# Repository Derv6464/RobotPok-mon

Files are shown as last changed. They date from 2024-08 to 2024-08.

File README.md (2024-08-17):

# Life Size Fuecoco Robot
This is a fully 3d printed robotic Fuecoco Pokemon. It can be controlled over wifi using a custom bulit contoller or a website

This was a college project for Immersive Software Engineering CS4445 and for a cosplay for Dubin Comic Con 2024.

The full project can be found on the college branch, it will include extra things like the website, interfacing with aws and a full report.

This branch has everything needed to 3d print and assemble the robot and control it using the custom controller.

## 3D Printing & laser cutting
This was printed using an Ender3 v2.
The model has been split up to fit in the 220mm * 220mm * 250mm build volume of the Ender3 v2
The orginal fuecoco model was found [here](#)

All the STL files can be found [here](#)

The top of the conrollet was laser cut from 3mm clear acrylic so the LEDs could shine through
This could be 3d printed if a laser cutter is not accessible

note the head has weird slots on the back, ingnore them and glue magnets instead

## Assembly

- 3d print all the parts
- do a lot of sanding and filling
- glue the parts together
- do more sanding and filling
- spray paint
- do more sanding and filling
- do the final coat of spray paint 
- assemble the electronics (see wiring diagram and code setup)
- put the electronics in the pokemon
- glue in the electornics
- glue on the magnets

## Wiring Diagram
tbd
solder pico headers up

## Code Setup
I used MicroPython on the Raspberry Pi Pico W
The code for the pokemon can be found [here](#)
Copy it over from the computer to the Raspberry Pi Pico W
Change the wifi ssid and password in the code
Run the code
The controller and fuecoco need to be on the same wifi network
fuecoco runs an api and the the controller sends requests to the api. When the fuecoco receives a request it moves the motors accordingly

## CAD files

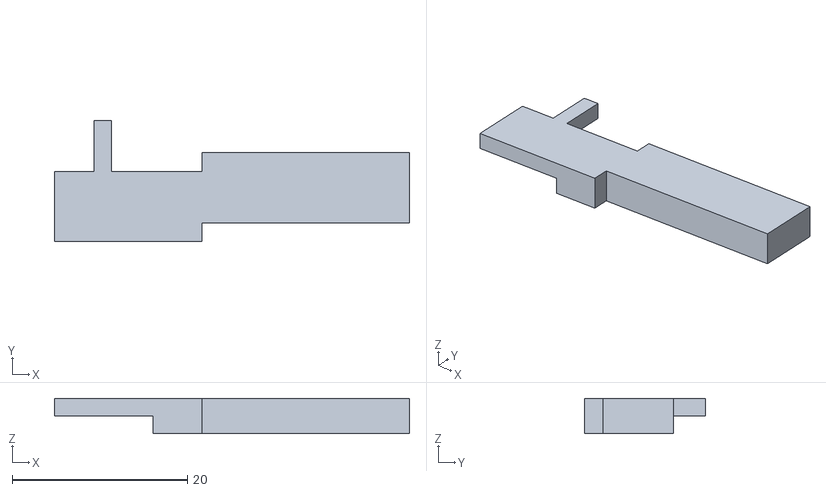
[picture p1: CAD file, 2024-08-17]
Controller/CAD/STL/TopAnalogStickHolder.stl
40.5 x 13.9 x 4.00

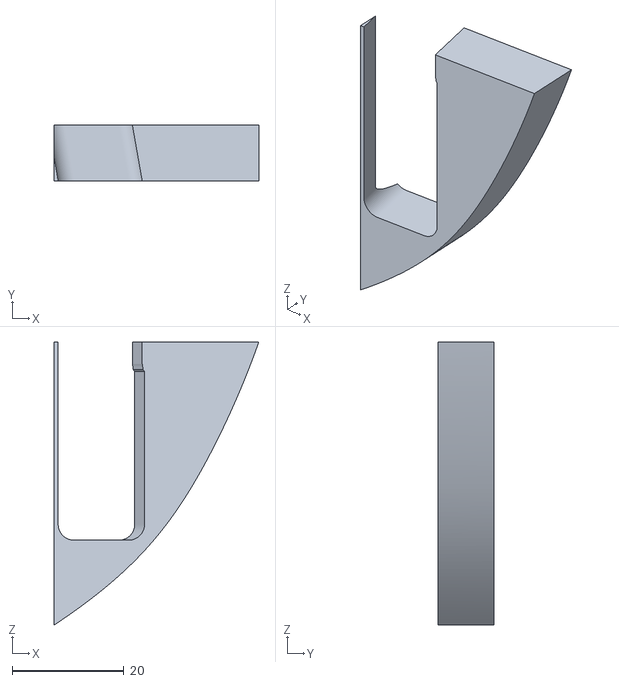
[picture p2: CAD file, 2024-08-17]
Fuecoco/CAD/STL/Tail 6AA battery holder p1.stl
36.6 x 10.0 x 50.6

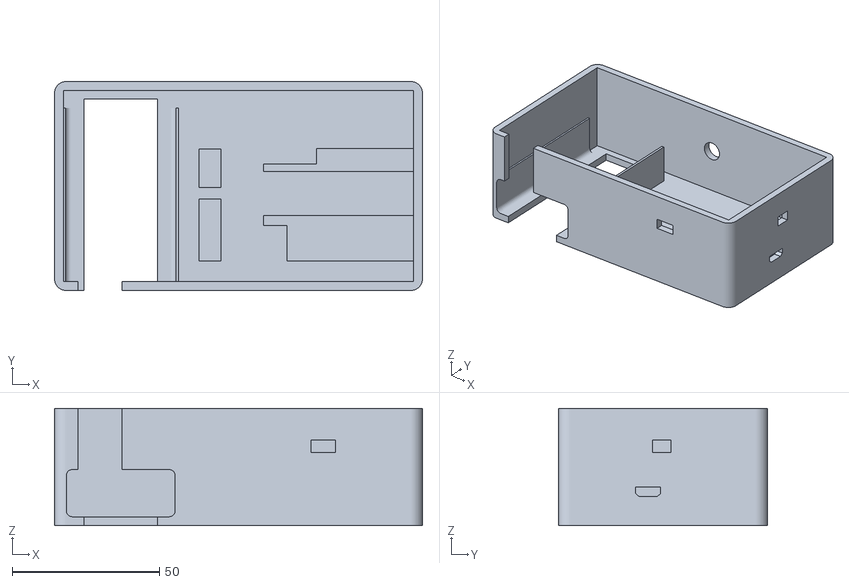
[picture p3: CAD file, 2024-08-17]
Controller/CAD/STL/ContollerBody.stl
125.0 x 71.0 x 39.8

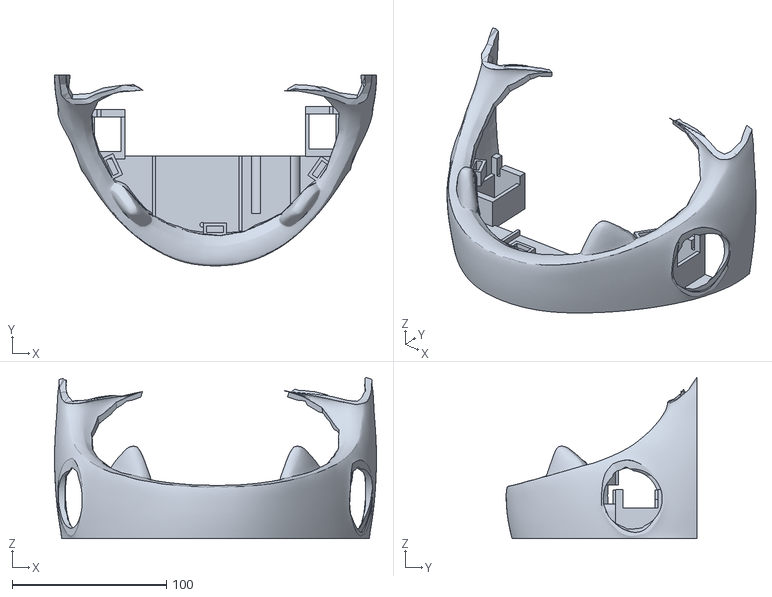
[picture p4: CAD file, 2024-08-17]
Fuecoco/CAD/STL/Chin.stl
209.0 x 123.8 x 104.6

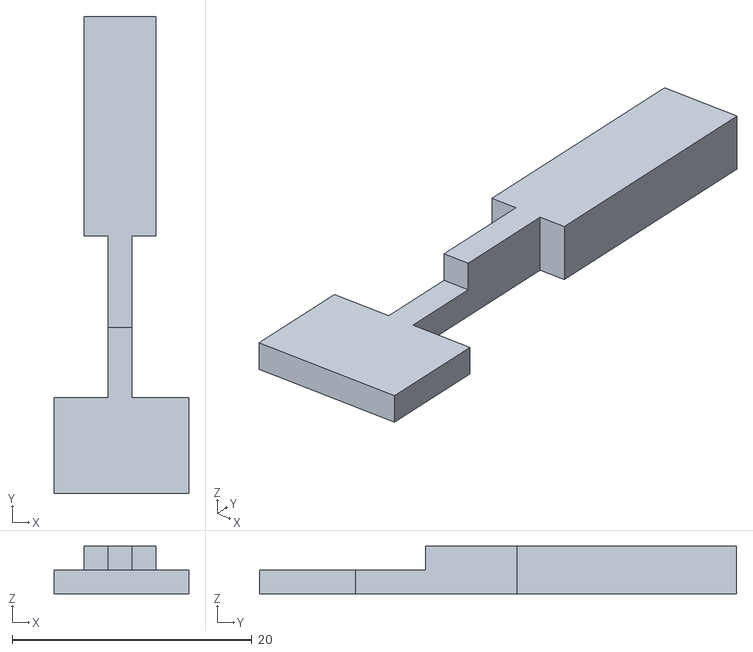
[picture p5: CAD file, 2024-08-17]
Controller/CAD/STL/BottomAnalogStickHolder.stl
11.2 x 39.8 x 4.00

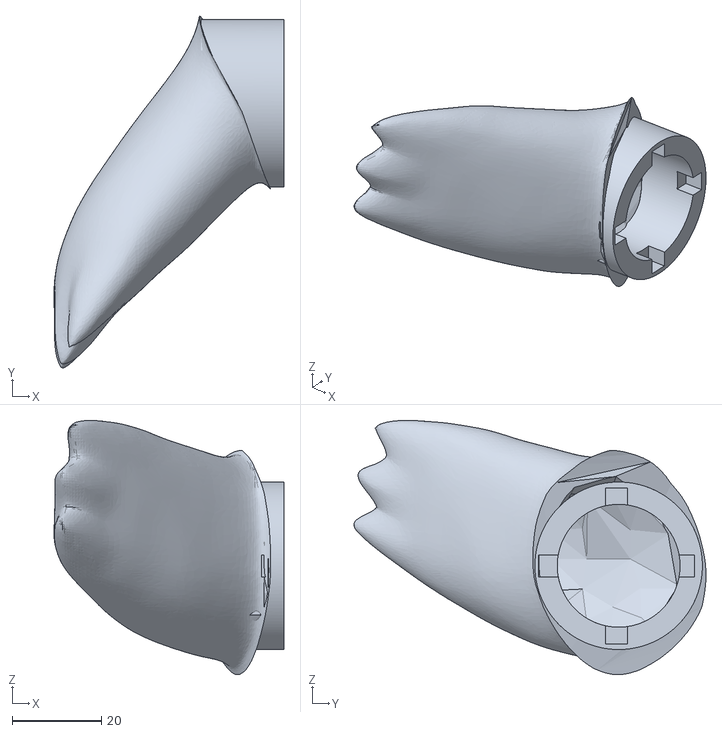
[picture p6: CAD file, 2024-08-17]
Fuecoco/CAD/STL/LeftArm.stl
51.4 x 78.8 x 56.9

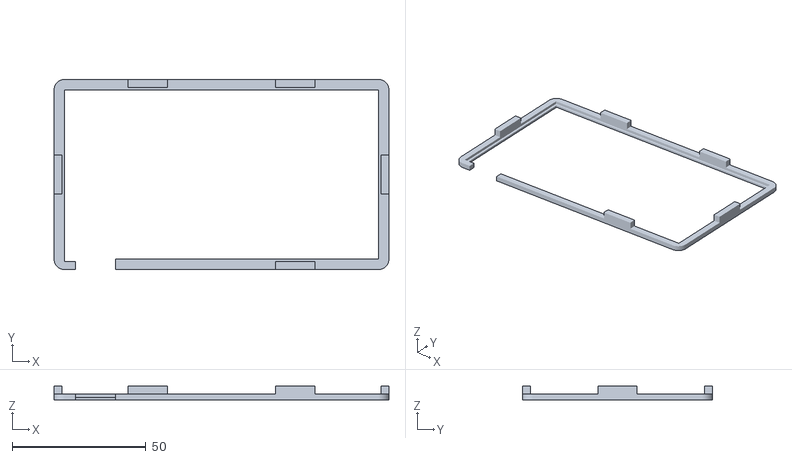
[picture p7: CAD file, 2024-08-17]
Controller/CAD/STL/nOOdHolder.stl
125.0 x 71.0 x 5.20

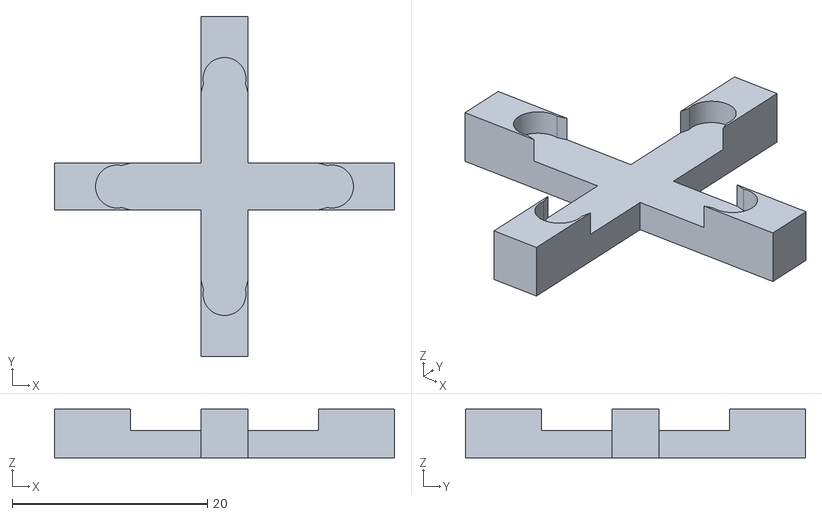
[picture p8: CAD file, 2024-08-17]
Fuecoco/CAD/STL/ArmToServo.stl
34.8 x 34.8 x 5.00

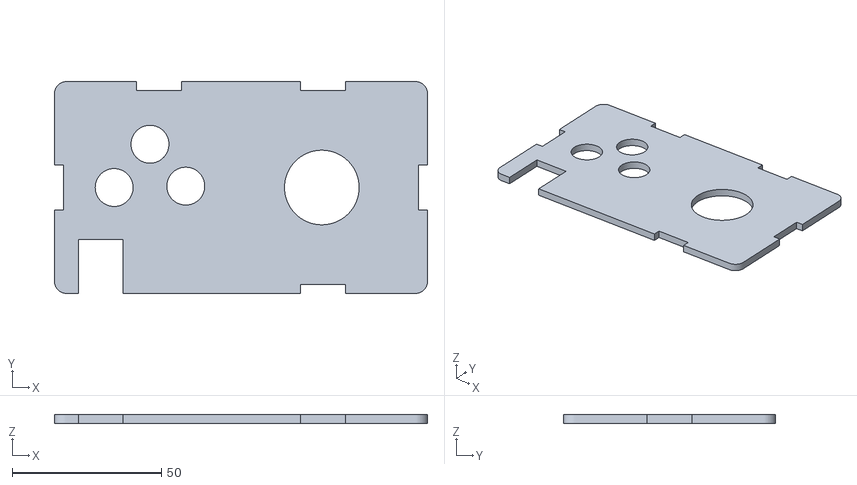
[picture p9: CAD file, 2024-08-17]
Controller/CAD/STL/Cover.stl
125.0 x 71.0 x 3.00

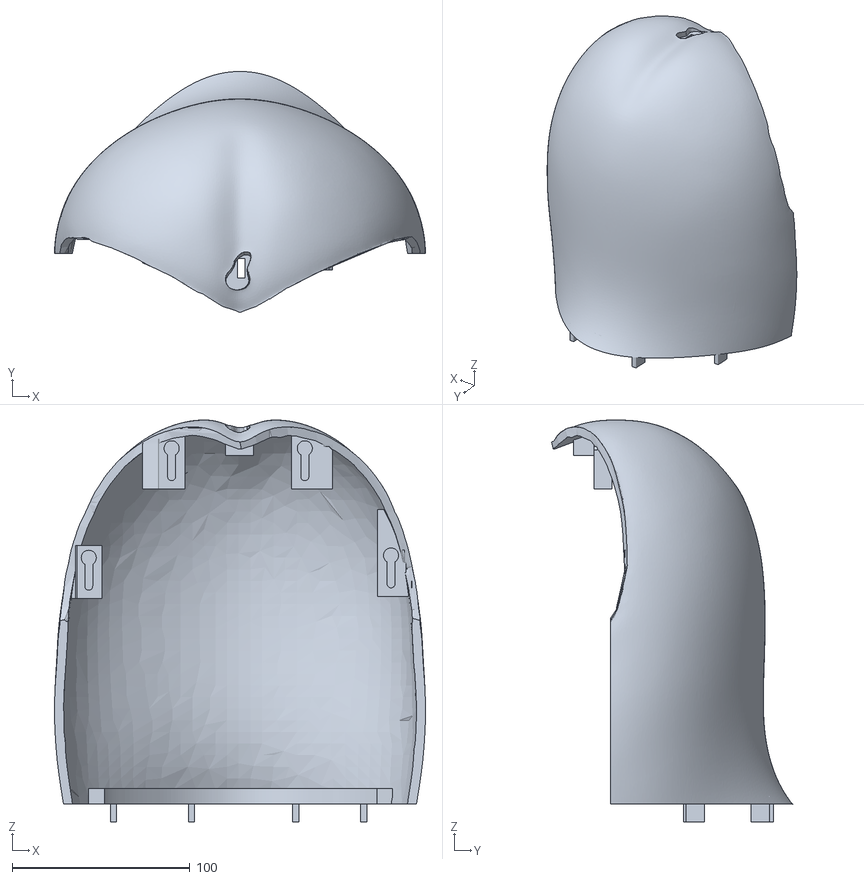
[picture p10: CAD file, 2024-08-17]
Fuecoco/CAD/STL/Body.stl
208.9 x 135.8 x 226.4

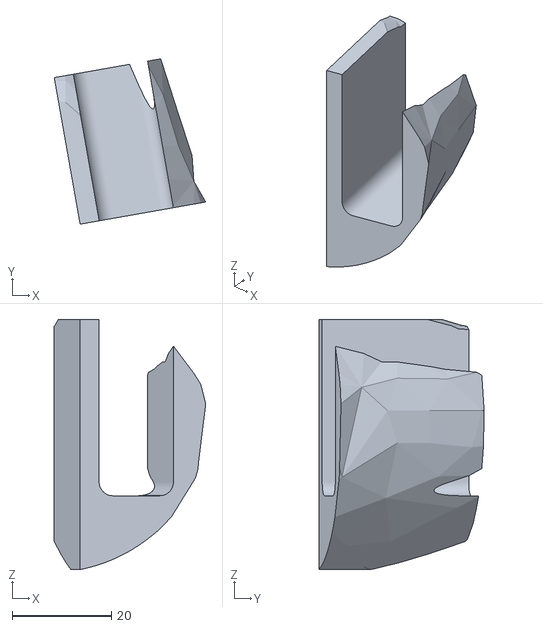
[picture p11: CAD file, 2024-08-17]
Fuecoco/CAD/STL/Tail 6AA battery holder p2.stl
30.5 x 33.3 x 50.4

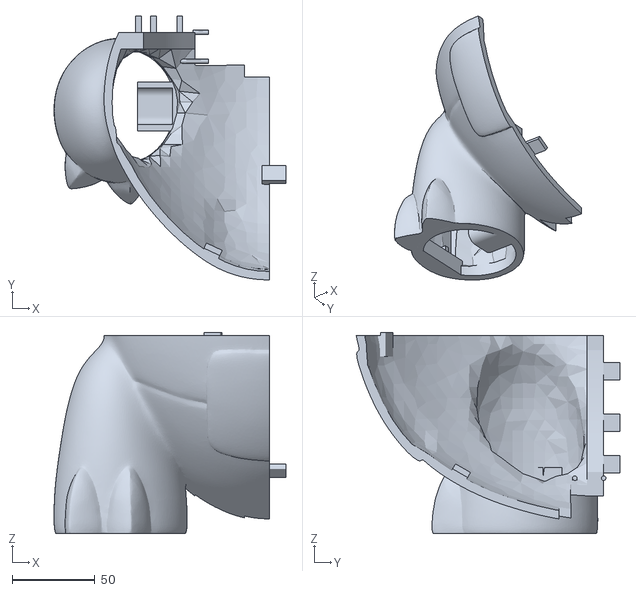
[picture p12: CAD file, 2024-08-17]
Fuecoco/CAD/STL/LeftLeg.stl
140.3 x 159.5 x 121.8

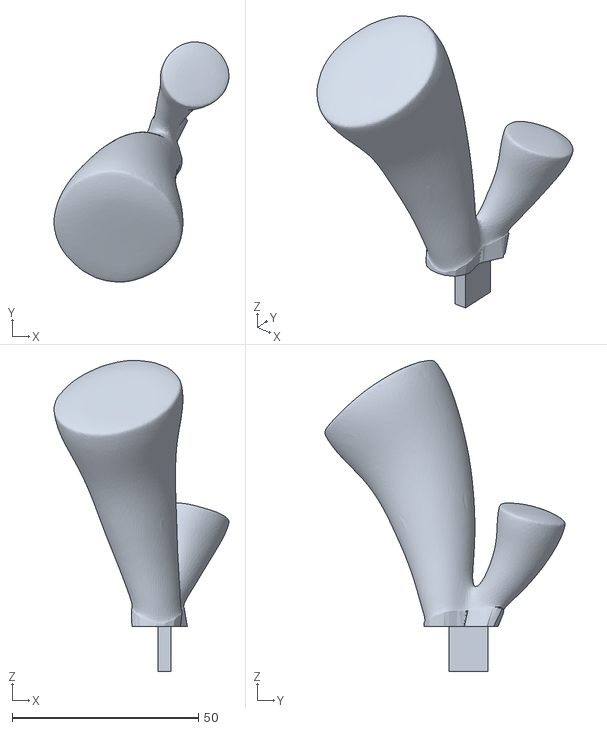
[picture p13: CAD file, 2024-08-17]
Fuecoco/CAD/STL/HeadFlame.stl
47.0 x 64.5 x 83.5

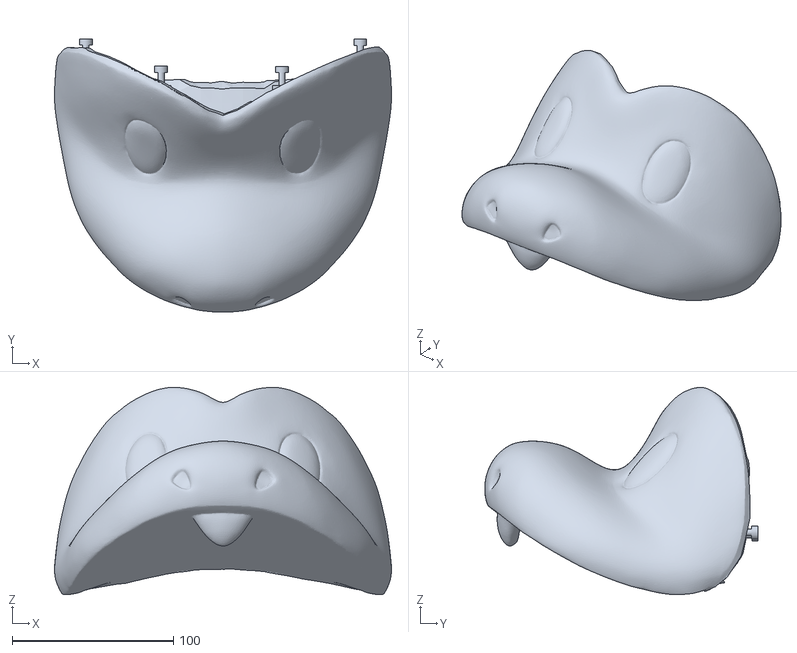
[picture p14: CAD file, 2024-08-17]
Fuecoco/CAD/STL/Head.stl
209.0 x 169.6 x 128.5

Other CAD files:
Fuecoco/CAD/STL/Tail.stl
Fuecoco/CAD/STL/RightLeg.stl
Fuecoco/CAD/STL/Tail 3AAA battery holder.stl
Fuecoco/CAD/STL/RightArm.stl
Controller/CAD/f3d/Controller.f3z

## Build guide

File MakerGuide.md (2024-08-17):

# How to make Fuecoco

## Parts

### Electronics

| Part | Quantity | Used in | link |
|---|---| ---| -----|
|Raspberry Pi Pico W| 2 | Pokemon and Controller | [Link](https://thepihut.com/products/raspberry-pi-pico-w) |
|Kitronik Motor Driver Board| 1 | Pokemon | [Link](https://kitronik.co.uk/products/5329-kitronik-compact-robotics-board-for-raspberry-pi-pico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) |
|Servo Motor| 2 | Pokemon | [Link](https://thepihut.com/products/towerpro-servo-motor-sg90-digital) |
|TT Hobby Motor| 3| Pokemon | [Link](https://thepihut.com/products/dc-gearbox-motor-tt-motor-200rpm-3-to-6vdc) |
| 6AA Battery Holder| 1 | Pokemon | [Link](https://www.digikey.ie/en/products/detail/mpd-memory-protection-devices/BH16AAW/857244) |
| 3AAA Battery Holder| 2 | Pokemon and Controller | [Link](https://thepihut.com/products/3-x-aaa-battery-holder-with-on-off-switch-and-2-pin-jst) |
|Neopixel Strip| 1 | Pokemon | [Link](https://thepihut.com/products/adafruit-neopixel-digital-rgb-led-strip-white-60-led-white) |4
| Buttons | 4 | Controller | [Link](https://www.mouser.ie/ProductDetail/Shin-Chin/R13-510A-05-BB?qs=F3UvtXhGJLNb6k88C5W3XA%3D%3D) |
| Joystick | 1 | Controller | Taken from broken controller |
| LEDs | 1 | Controller | Any |
| Light n00d | 1 | Controller | [Link](https://thepihut.com/products/noods-flexible-led-filament-3v-300mm-warm-white) |
| Solderable breadboard | 1 | Controller | [Link](https://thepihut.com/products/adafruit-perma-proto-half-sized-breadboard-pcb-single) |
| resistors | 1 | Controller | 330 ohm |

### Other Parts

| Part | Quantity | Used in | link |
|---|---| ---| -----|
| Lego Wheel | 3 | Pokemon | 
| Lego Wheel Holder | 3 | Pokemon |
| Lego Wheel Axle | 3 | Pokemon |
| Lego Wheel Axle Holder | 3 | Pokemon |
| LED Holder | 2 | Controller | 
| Magnets | 4 | Pokemon |
| Lots of hot glue | | Pokemon and Controller | Any |
| Lots of filler | | Pokemon | [Link](https://www.halfords.ie/motoring/paints-body-repair/fillers-preparation/holts-cataloy-knifing-putty-100g-154211.html) |
| Red spray paint | 1 | Pokemon | [Link](https://allcitygraffiti.com/products/red-madrid-94?variant=3243807178792) |
| Black spray paint | 1 | Pokemon | [Link](https://allcitygraffiti.com/products/black-94) |
| White spray paint | 1 | Pokemon | [Link](https://allcitygraffiti.com/products/white-94) |
| off white spray paint | 1 | Pokemon | [Link](https://allcitygraffiti.com/products/blanco-hueso-94) |
| yellow spray paint | 1 | Pokemon | [Link](https://allcitygraffiti.com/products/medium-yellow-94?variant=3243953881128) |
| light pink spray paint | 1 | Pokemon | [Link](https://allcitygraffiti.com/products/rosa-boreal-94?variant=3244061720616) |
| dark pink spray paint | 1 | Pokemon | [Link](https://allcitygraffiti.com/products/rosa-stereo-94?variant=3246509293608) |

All lego parts gotten from the lego mindstorms kit

## 3D Printing & laser cutting

It was just alot of sanding and filling, I spent about 40hr sanding and filling

1. 3d print all the parts (note these aren't the best models and have some issues)
print pic
2. do a lot of sanding and filling
sanding and filling pic
3. glue the legs, tail, body and chin together
glue pic
4. do more sanding and filling
sanding and filling pic
5. spray paint with primer
6. do more sanding and filling
7. do a coat of red colour
8. do more sanding and filling for any imperfections
9. do the final coat of spray paint

The order of the final coat colours I did was:

| Paint | Part| Colour |
|---|-----| ---|
|white primer everywhere| All | white |
|coat of red on body to see imperfections | Body | Red |
|bone white on the face | Head| Bone White |
|red on the arms | Arms | Red |
|light pink on the toungue | Tongue | Light Pink |
|white on the teeth, tape off| Head, Body  | White |
|sprayed the eyes with white, tape off | Head | White |
|sprayed the roof of the mouth dark pink, tape off | Head | Dark Pink |
|dark pink on the inner chin, lip area, tape off | Head | Dark Pink |
|sprayed the inner eyes with black, tape off | Head | Black |
|sprayed the nail area's of the feet with black, tape off | Body | Black |
|sprayed the square area's on the front and tail with yellow, tape off | Body | Yellow |
|bone white on the underbelly, tape off | Body | Bone White |
|red on the rest of the body| Body | Red |

But do whatever works

## Assembly

### Magnets

Orginall there was going to be a sloting system for the hesd to go on the body, hence the weird slots on the back of the head. I ended up glueing magnets in the head and body to hold it together.

I used the lower two slots, did a lot of sanding to make the magnets flush with the body and head and then glued them in with super glue, hot glue and then more super glue.

### Arms

1. The arms to servo parts should connect to a servo cross style servo horn. 
2. Glue these parts together.
3. The arm to servo part can then be sloted into the arms of the pokemon.
4. These should also be glued
5. The arms can be placed into the body, the servo's should be able to be slotted into the holders on the inside of the body

### Motor Assembly

This is not the easiest thing to do

#### Tail Motor

1. Create the lego structure for the motors, see photo
2. Place the dc motor to axel on the motors, they can be glued on if needed
3. Place the motor into the body, can be hot glued in
4. Place the lego structure into the body, have the thread loose around for now
5. Place the axels through the body and into the lego structure
6. Pull the thread around the wheels
7. Put on the red end caps

#### Leg Motors

1. Create the lego structure for the motors, see photo
2. Place the dc motor to axel on the motors, they can be glued on if needed
3. Connect the lego wheel to the motor
4. Place the motor into the body, can be hot glued in
5. Make sure wheel is slotted into gaps fully

### Battery holders

#### 3AAA Battery Holder

Can be glue into the body, on the left side of the tail

#### 6AA Battery Holder

The larger part can be glued deeper into the tail on the right side
The smaller part can be glued into the body on the right side, just before the connector lip

### Electronics

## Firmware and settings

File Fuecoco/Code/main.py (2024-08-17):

import connect as c
from microdot import Microdot
from cors import CORS
import PicoRobotics
import time
import machine
from neopixel import Neopixel
import urandom
import aws

ip = c.startUp()
print(ip)
#checking if the ip address has been updated from aws, not needed
#if aws.writeNew():
#    ip = c.startUp()
#    print(ip)
    
#aws.pushIP(c.getIP())


app = Microdot()
CORS(app, allowed_origins='*', allow_credentials=True)
board = PicoRobotics.KitronikPicoRobotics()
strip = Neopixel(96, 0, 28)
strip.brightness(100)


colour = {
    "red" : (0, 255, 0),
    "orange" : (100, 255, 0),
    "yellow" : (150, 255, 0),
    "green" : (255, 0, 0),
    "cyan" : (128, 0, 128),
    "blue" : (0, 0, 255),
    "purple" : (0, 128, 130),
    "null" : (0,0,0)
}

def changeNeopixel(color):
    strip.fill(colour[color])
    strip.show()
    time.sleep(0.001)

def forward():
    board.motorOn(1, "f", 100)
    board.motorOn(2, "r", 100)
    board.motorOn(3, "r", 100)
    
def stop():
    board.motorOn(1, "f", 0)
    board.motorOn(2, "f", 0)
    board.motorOn(3, "f", 0)
    
def backward():
    board.motorOn(1, "r", 100)
    board.motorOn(2, "f", 100)
    board.motorOn(3, "f", 100)
    
def left():
    board.motorOn(1, "f", 0)
    board.motorOn(2, "f", 100)
    board.motorOn(3, "r", 100)
    
def right():
    board.motorOn(1, "f", 0)
    board.motorOn(2, "r", 100)
    board.motorOn(3, "f", 100)
    
def arm():
    print("arms")
    board.servoWrite(1, 65)
    board.servoWrite(5, 30)
    time.sleep(0.5)
    board.servoWrite(1, 90)
    board.servoWrite(5, 25)
    time.sleep(0.5)
    board.servoWrite(1, 55)
    board.servoWrite(5, 50)
    time.sleep(0.5)
    board.servoWrite(1, 65)
    board.servoWrite(5, 30)
    board.adjustServos(0)
    
def leftArm():
    print("left")
    board.servoWrite(5, 30)
    time.sleep(0.5)
    board.servoWrite(5, 25)
    time.sleep(0.5)
    board.servoWrite(5, 50)
    time.sleep(0.5)
    board.servoWrite(5, 30)
    time.sleep(0.5)
    board.adjustServos(0)

def rightArm():
    print("right")
    board.servoWrite(1, 65)
    time.sleep(0.5)
    board.servoWrite(1, 90)
    time.sleep(0.5)
    board.servoWrite(1, 55)
    time.sleep(0.5)
    board.servoWrite(1, 65)
    time.sleep(0.5)
    board.adjustServos(0)
    
def fl():
    board.motorOn(1, "f", 100)
    board.motorOn(2, "r", 10)
    board.motorOn(3, "r", 100)
    
def fr():
    board.motorOn(1, "f", 100)
    board.motorOn(2, "r", 100)
    board.motorOn(3, "r", 20)

def bl():
    board.motorOn(1, "r", 100)
    board.motorOn(2, "f", 10)
    board.motorOn(3, "f", 100)
    
def br():
    board.motorOn(1, "r", 100)
    board.motorOn(2, "f", 100)
    board.motorOn(3, "f", 20)

    
def bounds(value, min_val, max_val):
    return max(min(value, max_val), min_val)


def fire():
    start = time.time()
    end = 2
    while (time.time()-start) < end:
        r = 255
        g = 80
        b = 20

        #Flicker, based on our initial RGB values
        for i in range (0, 96):
            flicker = urandom.randint(0,110)
            r1 = bounds(r-flicker, 0, 255)
            g1 = bounds(g-flicker, 0, 255)
            b1 = bounds(b-flicker, 0, 255)
            strip[i] = (g1,r1,b1)
        strip.show()
        time.sleep(0.1)
    changeNeopixel("null")
    
@app.route('/stop', methods=['POST'])
def motorOn(request):
    print('connented')
    stop()
    return "done"

@app.route('/mu', methods=['POST'])
def motorOn(request):
    print('connented')
    forward()
    return "done"

@app.route('/md', methods=['POST'])
def motorOff(request):
    print('connented')
    backward()
    return "done"

@app.route('/lm', methods=['POST'])
def motorOff(request):
    print('connented')
    left()
    return "done"

@app.route('/lu', methods=['POST'])
def motorOff(request):
    print('connented')
    fl()
    return "done"

@app.route('/ld', methods=['POST'])
def motorOff(request):
    print('connented')
    bl()
    return "done"

@app.route('/rm', methods=['POST'])
def motorOff(request):
    print('connented')
    right()
    return "done"

@app.route('/ru', methods=['POST'])
def motorOff(request):
    print('connented')
    fr()
    return "done"

@app.route('/rd', methods=['POST'])
def motorOff(request):
    print('connented')
    br()
    return "done"

@app.route('/al', methods=['POST'])
def motorOff(request):
    print('connented')
    leftArm()
    return "done"

@app.route('/ar', methods=['POST'])
def motorOff(request):
    print('connented')
    rightArm()
    return "done"

@app.route('/ab', methods=['POST'])
def motorOff(request):
    print('connented')
    arm()
    return "done"

@app.route('fire',methods=['POST'])
def motorOff(request):
    print('connented')
    fire()
    return "done"

print('running app')
app.run(port=80)

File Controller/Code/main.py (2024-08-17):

import inputs
import outputs
import connect as c
from machine import Pin
import time


stick = inputs.AnalogStick(26,27)
b1 = Pin(20, Pin.IN, Pin.PULL_DOWN) #purple
b2 = Pin(19, Pin.IN, Pin.PULL_DOWN) #yellow
b3 = Pin(18, Pin.IN, Pin.PULL_DOWN) #orange
b4 = Pin(28, Pin.IN, Pin.PULL_DOWN) 
c.startUp()
#check aws for new ip/wifi

while True:
    time.sleep(0.2)
    direction = stick.getDir()
    if direction != ["m","m"]:
        print(direction[0],direction[1])
        print(outputs.moveLegs(direction))
        #time.sleep(0.1)
    elif b1.value():
        print("right")
        outputs.moveArms("r")
        time.sleep(2)
    elif b2.value():
        print("left")
        outputs.moveArms("l")
        time.sleep(2)
    elif b3.value():
        print("both")
        outputs.moveArms("b")
        time.sleep(2)
    elif b4.value():
        print("fire")
        outputs.breatheFire()
        time.sleep(1)
    else:
        outputs.stop()
    #c.checkConnection()

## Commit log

2024-08-17 Adding cad
    [ArmToServo.stl, Body.stl, Chin.stl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]
2024-08-17 Adding controller CAD
    [BottomAnalogStickHolder.stl, ContollerBody.stl, Controller.f3z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]
